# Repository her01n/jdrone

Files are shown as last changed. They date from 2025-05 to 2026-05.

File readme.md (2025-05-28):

jdrone is a printable model for a quadcopter frame.
The model is designed programatically using
[jscad](https://github.com/jscad/OpenJSCAD.org) library.

The parts are designed to be easy to print.
No support is necessary, bridges and overhangs are kept short.
The build plate of 120x120 mm is necesary.
I recommend to print the parts with ABS.

We use M3x4x5 thread inserts and M3x8 button head screws
to connect the parts of the frame.
All parts are connected with minimum of two screws.
The motors are also connected with M3x8 screws.
The stack connects with four M3x20 button head screws.

The quadcopter is measured about 257mm diagonally,
and can handle propellers with 180mm diameter.
The motors are attached by 16*16mm M3 screws.
Flight controller is installed in 30.5x30.5mm or 20x20mm mounting, installing the stack is possible.
Receiver with dimensions 16x11mm can be added.

## Layout preview

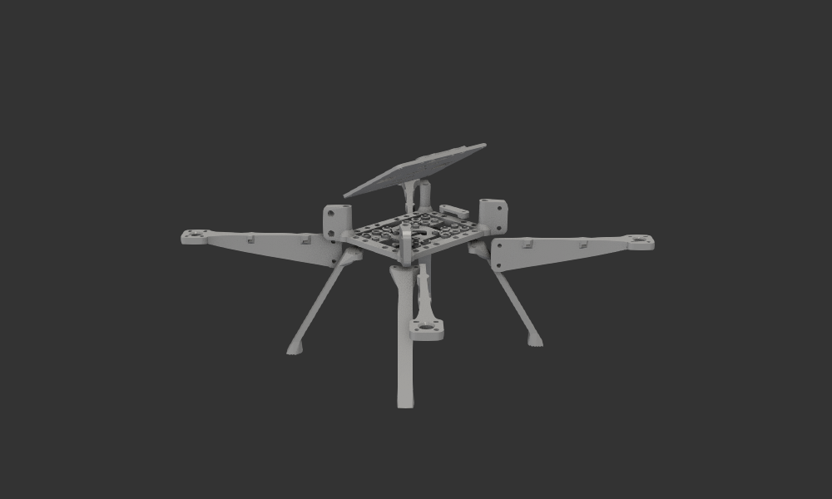
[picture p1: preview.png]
Layout preview


[View 3d model.](https://github.com/her01n/jdrone/blob/main/stl/preview.stl)

## BOM

Printed parts

- 1x core
- 1x top
- 4x arm
- 4x long-leg-d

Connectors

- 20x M3x5x4 thread inserts. Thread M3, outer diameter 5mm, length 4mm.
- 24x M3x8 button head screws. Thread M3, length 8mm. Any head if not countersunk should work.
- 4x M3x25 button head screws.

Other parts necessary depends on the stack and optionally radio used:

### 20mm stack

- 1x flight controller and 1x ESC with 4 mounting holes of 3mm diameter,
  layed out in a square with a 20mm long side.
- 4x M2x4x3.2 thread set inserts. Inner diameter is 2mm, length 4mm and outer diameter 3.2mm.
- 8x M2/M3 silicone pads, 6-7mm long
- 4x M2x16 screws

### 30.5mm stack

- 1x flight controller and 1x ESC with 4 mounting holes of 4mm diameter,
  layed out in a corners of a square with 30.5mm long side.
- 8x M3/M4 silicone pads, 8mm long.
- 4x M3x5x4 thread inserts.
- 4x M3x20 button head screws.

### 16x11 mm radio

- 1x pcb radio with dimensions 16x11mm.
- 2x M3x5x4 thread inserts
- 2x M3x8 screws

## Gopro

It's possible to add a mount for a gopro or similar action camera.

Additional parts needed:

- 2x M3x5x4 thread inserts.
- 1x M5x7x8 thread insert.
- 2x M3x8 screws.

Print *gopro* model with ABS.
Optionally print *gopro-pad* with flexible material, like TPU.

## Usb

Model *usb* contains two parts that could be used to fix a usb-a socket.
It can be used to hold a wifi usb adapter for digital fpv.
The usb can be fixed to *core*, *top* or *horns* part.

Additional parts needed:

- 4x M3x5x4 thread inserts
  Two inserts in *usb* part and two in *core*, *top* or *horns*.
- 4x M3x8 screws

## Compile

Install *node*, *make* and *@jscad/cli* package, example for arch:

```
sudo pacman -Syu --needed npm make
sudo npm install -g @jscad/cli
```

Now you can run *make* to generate *stl* files.

```
make
```

## Photo

GOPR0438

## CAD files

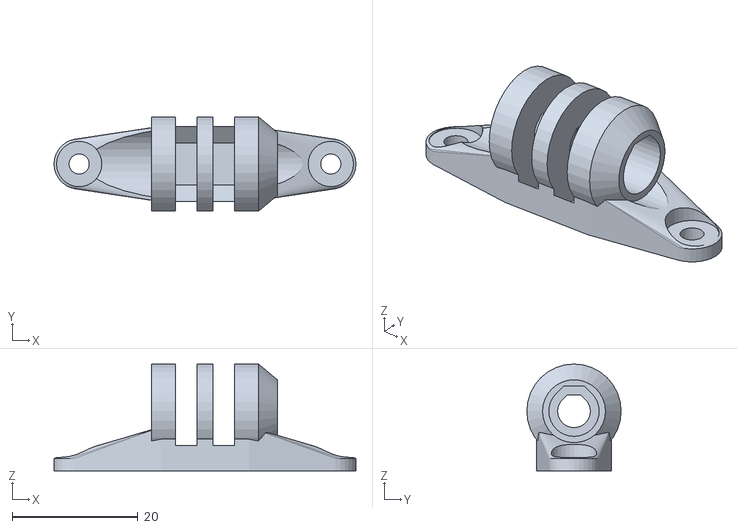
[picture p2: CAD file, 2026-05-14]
stl/gopro.stl
48.0 x 15.0 x 17.0

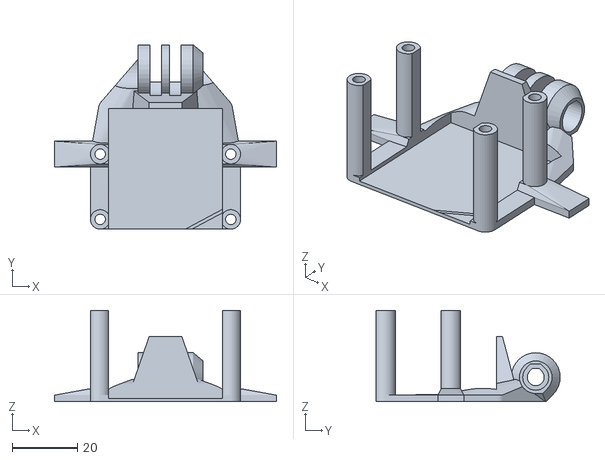
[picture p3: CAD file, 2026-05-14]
stl/belly-gopro.stl
68.0 x 56.5 x 28.0

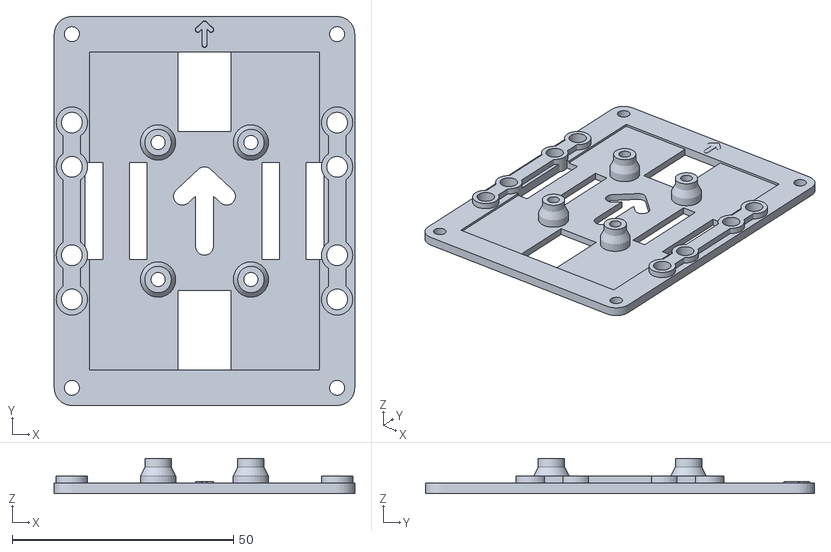
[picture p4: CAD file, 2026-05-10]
stl/top-gps.stl
68.0 x 88.0 x 8.00

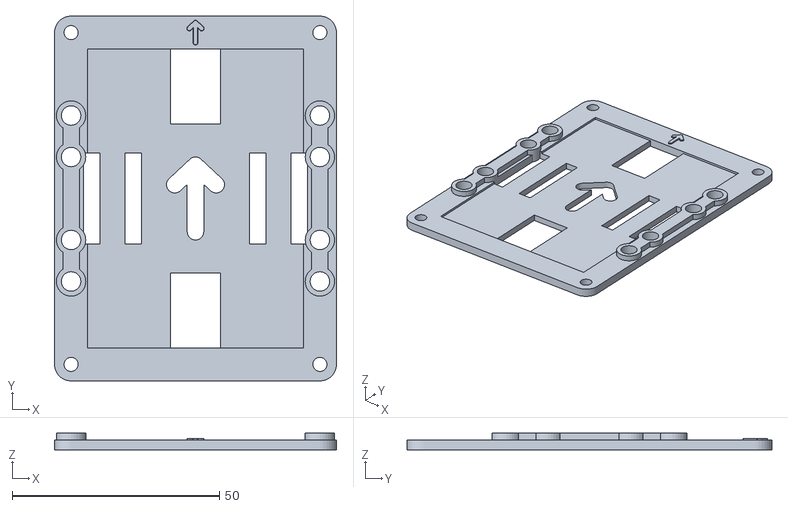
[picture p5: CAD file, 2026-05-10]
stl/top.stl
68.0 x 88.0 x 4.00

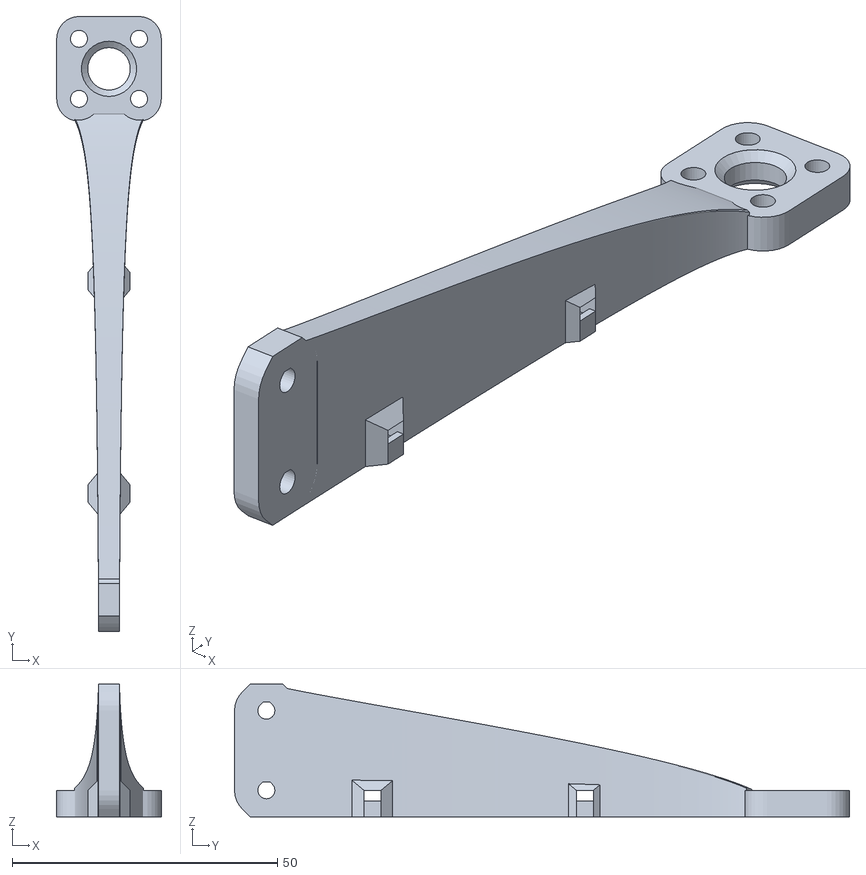
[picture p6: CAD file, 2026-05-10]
stl/arm.stl
19.7 x 115.9 x 25.0

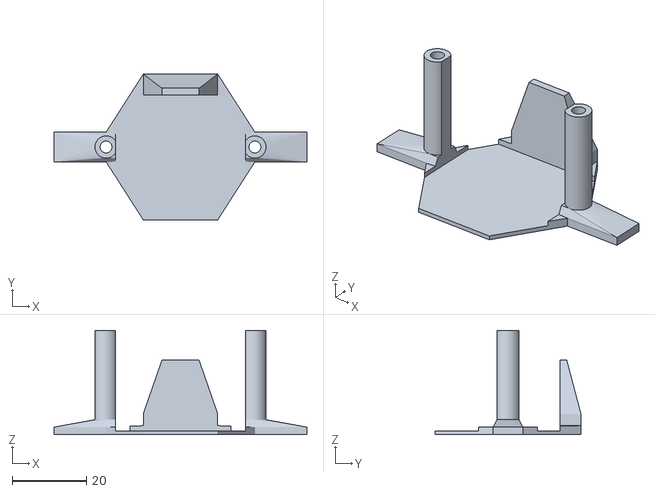
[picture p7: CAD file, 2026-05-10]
stl/belly.stl
68.0 x 39.2 x 28.0

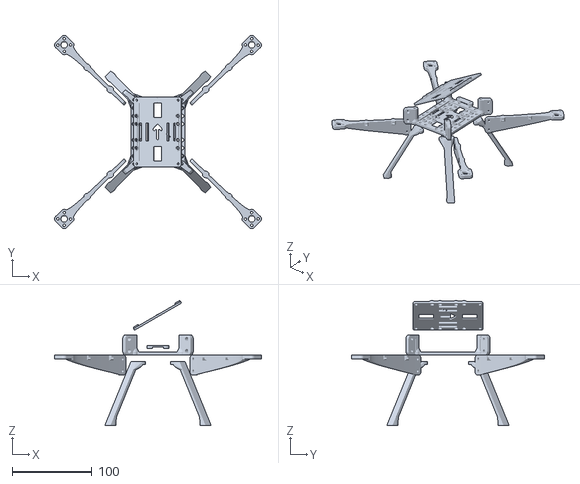
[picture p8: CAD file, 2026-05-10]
stl/preview.stl
259.1 x 242.1 x 156.5

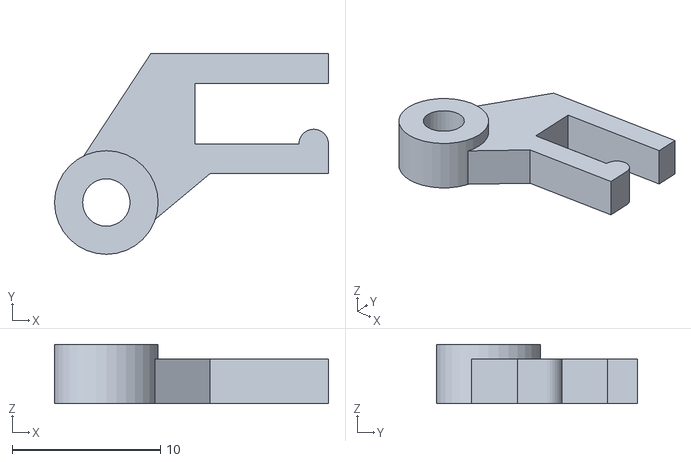
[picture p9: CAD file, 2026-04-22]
stl/antenna.stl
18.5 x 13.5 x 4.00

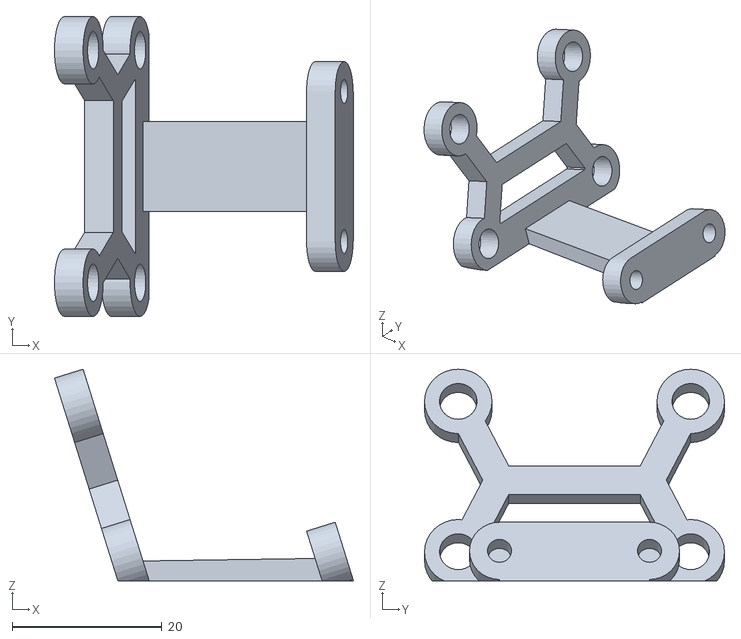
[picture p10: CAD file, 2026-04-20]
stl/gps-stem.stl
39.9 x 40.0 x 28.2

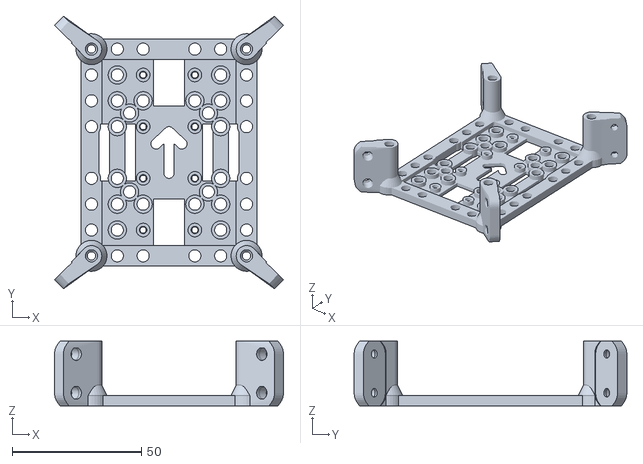
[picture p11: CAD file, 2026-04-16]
stl/core.stl
88.6 x 105.5 x 25.0

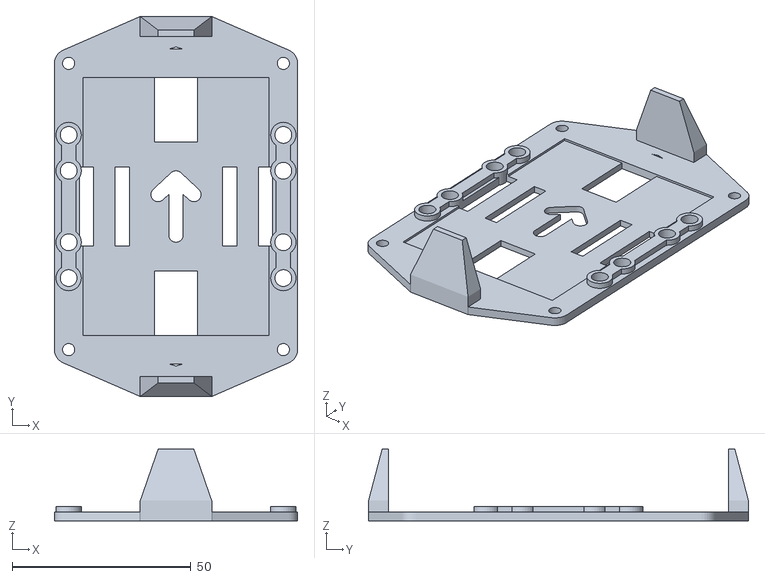
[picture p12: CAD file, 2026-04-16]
stl/horns.stl
68.0 x 106.2 x 20.0

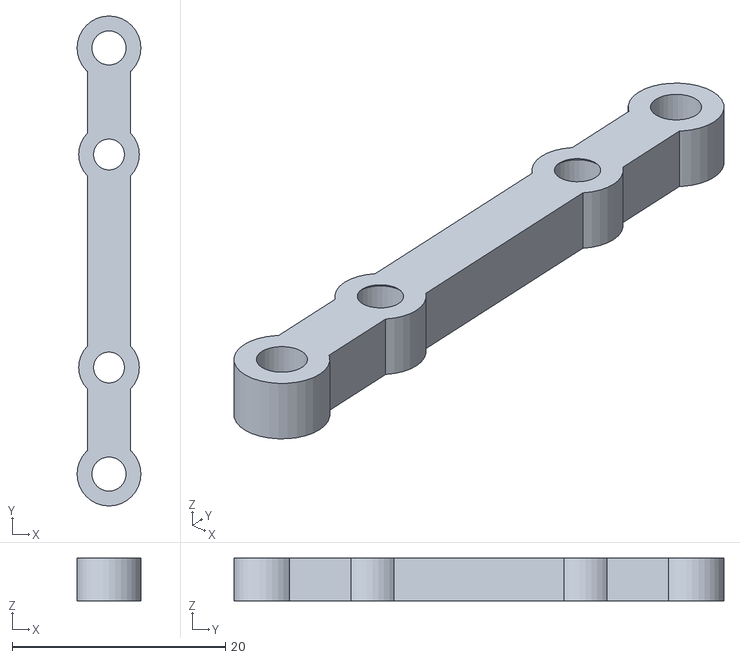
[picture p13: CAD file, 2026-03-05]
stl/magnetometer.stl
6.00 x 46.0 x 4.00

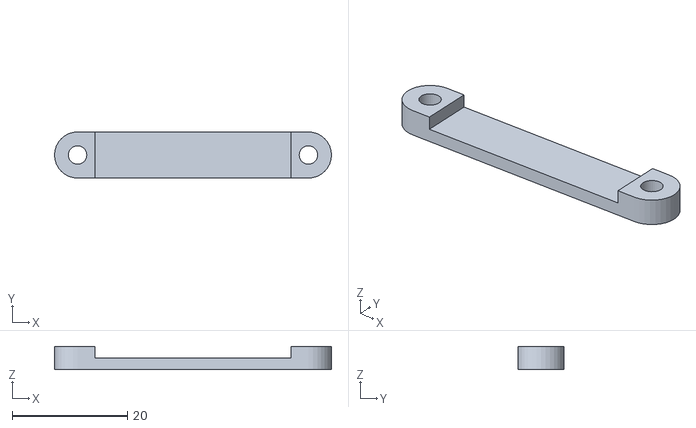
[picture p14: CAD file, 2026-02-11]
stl/bind40.stl
48.0 x 8.00 x 4.00

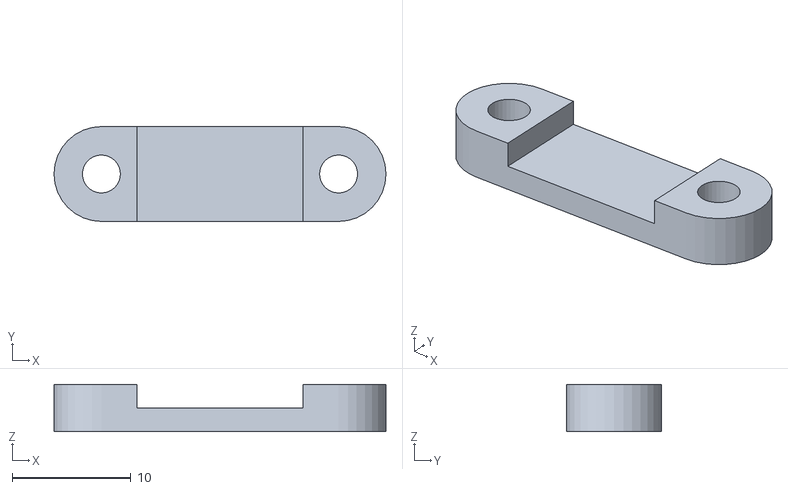
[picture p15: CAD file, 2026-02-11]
stl/bind20.stl
28.0 x 8.00 x 4.00

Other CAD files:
stl/strap.stl
stl/pi-camera.stl
stl/long-leg-d.stl
stl/belly-camera-screw.stl
stl/gopro-pad.stl
stl/long-leg-c.stl

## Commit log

2024-09-18 replace two types of legs with one type of diagonal legs
    [long-leg-d.stl, long-leg-s.stl, long-leg-w.stl]
2024-10-06 add layout preview
    [preview.stl, rx.stl]
2024-10-06 add screws info to readme
2024-11-06 move arm thread inserts to the surface
    [center.stl, preview.stl]
2024-11-06 less tall center
    [center.stl, preview.stl]
2024-11-06 narrower center
    [center.stl, preview.stl, top.stl]
2024-11-07 add thread inserts for 20mm stack
    [core.stl, preview.stl]
2024-11-07 longer thread inserts in pillars to allow for reinforcement screws
    [core.stl, preview.stl]
2024-11-07 some space for arm screws
    [core.stl, preview.stl]
2024-11-30 fit 25mm reinforcement screw
    [preview.stl, top.stl]
2024-11-30 make top as wide as pillars
    [preview.stl, top.stl]
2024-11-30 add 20mm strip to the top
    [preview.stl, top.stl]
2024-12-02 stronger arm connection
    [core.stl, preview.stl]
2024-12-03 support 20mm stack
    [core.stl, preview.stl]
2024-12-18 use only M3x5x4 thread inserts
    [core.stl, preview.stl, top.stl]
2024-12-18 add gopro pad
    [gopro-pad.stl]
2025-01-21 gopro holder
    [gopro.stl]
2025-01-28 fix gopro thread insert length
    [gopro.stl]
2025-04-23 bigger core
    [core.stl, long-leg-c.stl, long-leg-d.stl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]
2025-04-25 add pi camera box
    [pi-camera.stl, preview.stl]
2025-05-28 feature: usb
    [horns.stl, top.stl, usb.stl]
2025-11-14 gopro holder: make thread insert easier
    [gopro.stl]
2025-11-24 return to rectangular core
    [core.stl, horns.stl, preview.stl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]
2026-01-12 replace eyelets with removable straps
    [arm.stl, preview.stl, strap.stl]
2026-02-11 simplify rx and usb with bind
    [bind20.stl, bind40.stl, preview.stl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]
2026-03-05 adafruit magnetometer module
    [horns.stl, magnetometer.stl]
2026-03-24 allow to install rx on top
    [horns.stl, top.stl]
2026-04-20 stronger arms
    [arm.stl, preview.stl]
2026-04-21 even stronger arm
    [arm.stl, preview.stl]
2026-04-22 allow the gps to be installed on the top directly
    [gps-flat.stl, gps-stem.stl, horns.stl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]
2026-04-22 add antenna holder
    [antenna.stl]
2026-05-10 more flexible arm
    [preview.stl]
2026-05-10 belly with screw camera mount
    [arm.stl, belly-camera-screw.stl, belly.stl]
2026-05-10 gps on top as a single piece
    [gps-flat.stl, gps.stl, horns.stl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]
2026-05-13 add belly with gopro mount
    [belly-camera-screw.stl, belly-gopro.stl, gopro.stl]
2026-05-14 fix the gopro orientation
    [belly-gopro.stl, gopro.stl]
